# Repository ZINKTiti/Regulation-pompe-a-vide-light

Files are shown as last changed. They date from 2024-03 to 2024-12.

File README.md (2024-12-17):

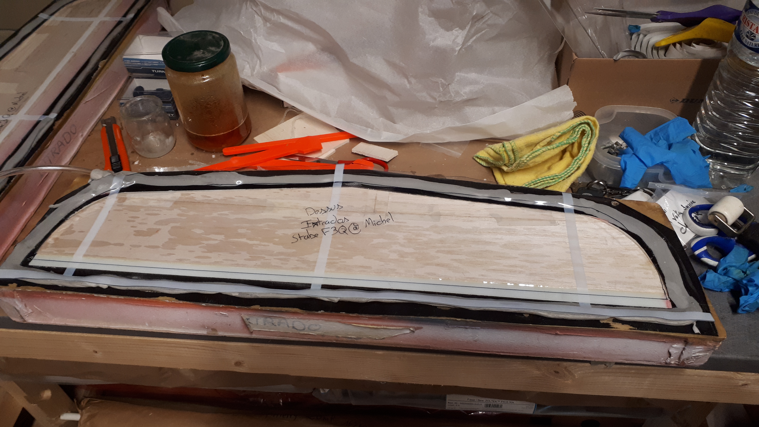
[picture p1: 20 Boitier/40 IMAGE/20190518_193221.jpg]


# ENGLISH

## Vaccum regulation

This is a light way to manage the vaccum pump to mold composit model aircraft

:warning: WARNING :warning: |
:--:|
**This assembly includes 220V connections. Take all safety measures to avoid any electrical shock that could cause irreversible bodily harm or even death.**|
**Never work on your assembly while it is live.**|

You can found the wiki  [Here](https://github.com/ZINKTiti/Regulation-pompe-a-vide-light/wiki)
The original is comming from [This](https://www.rcgroups.com/forums/showthread.php?2617244-Arduino-vacuum-pump-controller/page2)

---
---

# FRENCH

## Régulation de pompe a vide

Ce montage est un moyen de reguler le vide pour le moulage sous vide de model réduit

:warning: ATTENTION :warning: |
:--:|
**Ce montage comporte des connections en 220V. Prenez toutes les mesures de sécurité afin d'éviter tous choque éléctrique pouvant entrainer des domages corporels ireversible voir entrainer la mort**|
**Ne jamais intervenir sur votre montage sous tension**|

Vous pouvez trouver le wiki [ICI](https://github.com/ZINKTiti/Regulation-pompe-a-vide-light/wiki)
L'idée original viens de ce [cite](https://www.rcgroups.com/forums/showthread.php?2617244-Arduino-vacuum-pump-controller/page2)

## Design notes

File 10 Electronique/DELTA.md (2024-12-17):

# V1

Ajouter |
:--:|
Ajout de deux support à fusible protection primaire et secondaire|

Modifier |
:--:|
changement de Pin pour le DT de Pin4 à Pin3|
changement de Pin pour le CLK de Pin3 à Pin2|

Supprimer |
:--:|
|

# V0

Premire version

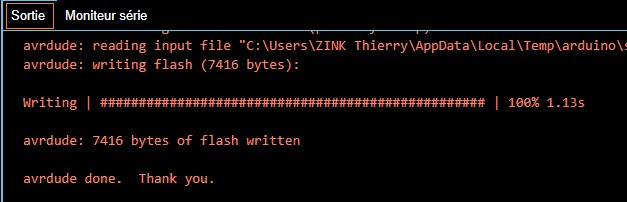
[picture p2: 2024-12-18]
25 Document/Chargement Fini.jpg

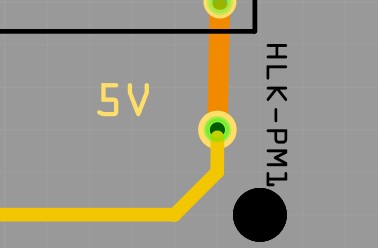
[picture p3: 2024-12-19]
25 Document/PCB_passage1.jpg

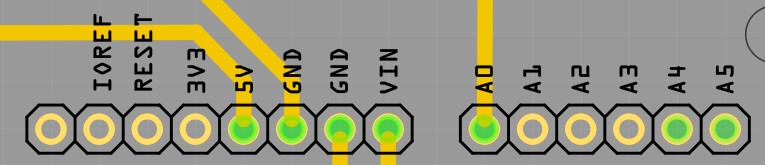
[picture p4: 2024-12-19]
25 Document/PCB_connecteur Arduino1.jpg

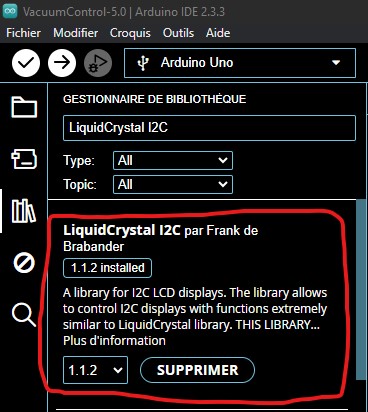
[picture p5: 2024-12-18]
25 Document/Liquid crystal Frank de brabander.jpg

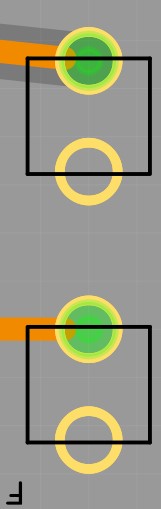
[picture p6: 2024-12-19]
25 Document/PCB_F1.jpg

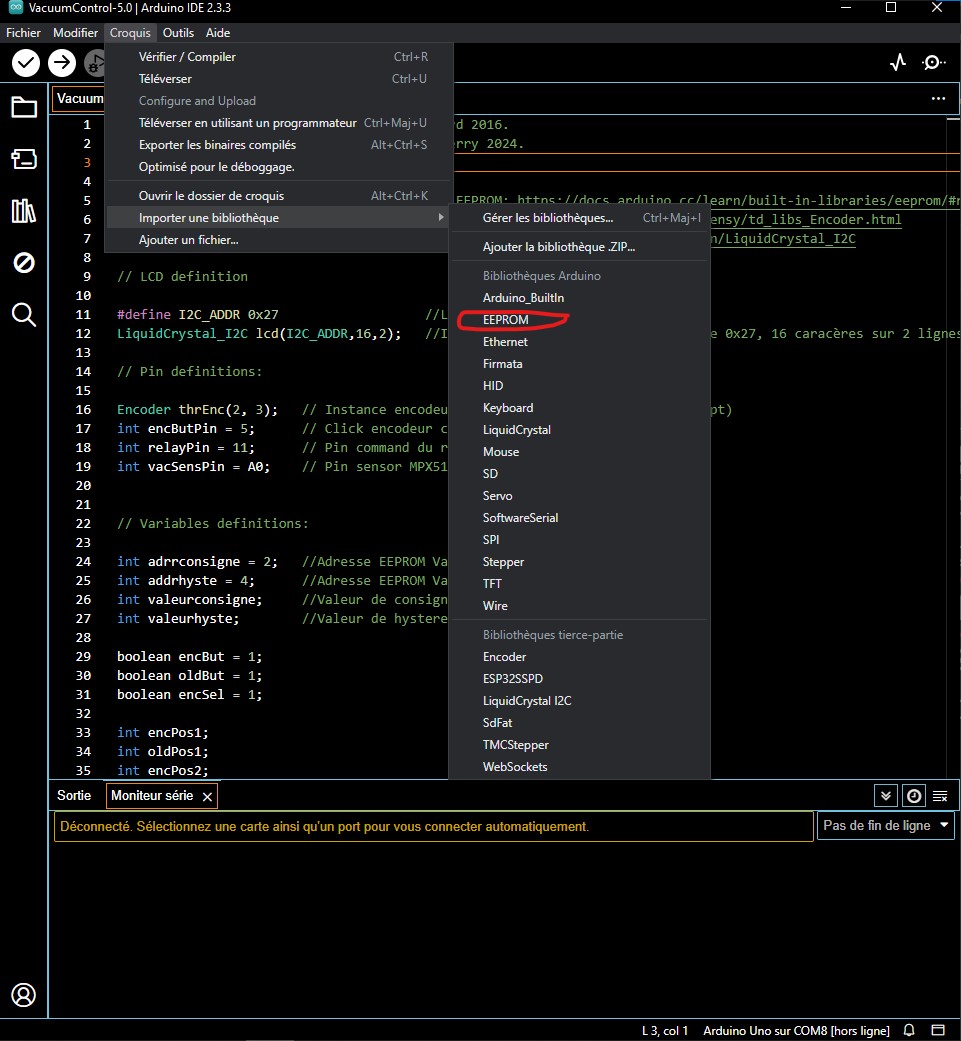
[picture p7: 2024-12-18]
25 Document/EEPROM.jpg

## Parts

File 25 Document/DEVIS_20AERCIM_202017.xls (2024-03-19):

Bruno REY |  |  |  |  |  |  | Devis
Bruno REY, AERCIM |  |  |  |  |  | le |  | N°
40 rue de la Providence
31500 | TOULOUSE
Téléphone | 05 61 20 69 57
 | 06 87 59 65 15
Email | aercim.ci@gmail.com
SIRET ; 803201680-00011 RM – RCS Toulouse
TVA non applicable, art 293B du CGI |  |  |  |  |  | www.aercim.com
toutes factures d'un montant inférieur à 100 euros sont à régler à la fin du mois en cours
 |  |  |  |  |  |  |  | d'avance merci
V/Réf: N°Cde:
Référence | Q | Nb Face | Dimensions |  | Trous | Descriptions |  | P.U | Montant
 | 4 | 2 | 10 | 6.7 | 62 |  |  | 7.02 | 28.09
 | 1 |  |  |  |  |  |  | 0.00 | 4.00
 |  |  |  |  |  | Frais de port/paypal |  |  | 3.00
 | Tarif surface |  | SF | 8 | euro/dcm² |  | Total |  | 35.09 | €
 | 2.7 | dm² | DF | 9 | euro/dcm² |  | acompte
 |  |  |  |  | franchise de TVA ; art 293B du CGI
chèques ; à l'ordre de Bruno REY |  |  |  |  |  |  | Total à régler |  | 35.09 | €
virement ; demander un RIB
paypal ; demande de paiement par email
 |  |  |  | Règlement
 |  |  |  | Échéance
En cas de retard de paiement, indemnité forfaitaire légale pour frais de recouvrement : 40,00 €
AERCIM : une électronique selon vos besoins.
Tout ou partie de votre projet ;
Du cahier des charges au produit fini, nous savons le faire.

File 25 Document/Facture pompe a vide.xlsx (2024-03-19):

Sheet: Sylvain
Pompe a vide
Designation | Prix unitaire | Quantité | Prix
CI | 13.25 | 1 | 13.25
MPX5100DP | 14.11 | 1 | 14.11
Aduino Uno | 8.99 | 1 | 8.99
2 pole | 1.43 | 1 | 1.43
Relais Statique | 9.8 | 1 | 9.8
LCD | 4.42 | 1 | 4.42
HLK-PM01 | 3.998 | 1 | 3.998
HY-040 | 2.3484 | 1 | 2.3484
Cable + prise | 5 | 1 | 5
Prise de courant | 3.9 | 1 | 3.9
Bois | 7.7 | 1 | 7.7
 |  |  | 0
Temps | 10 | 1 | 10
 |  |  | 0
 |  |  | 0
 |  |  | 0
 |  |  | 0
Total |  |  | 84.9464

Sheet: Jean Luc
Pompe a vide
Designation | Prix unitaire | Quantité | Prix
CI | 13.25 | 1 | 13.25
MPX5100DP | 13.99 | 1 | 13.99
Aduino Uno | 6.6 | 1 | 6.6
2 pole | 0.75 | 1 | 0.75
Relais Statique | 3.69 | 1 | 3.69
LCD | 4.34 | 1 | 4.34
HLK-PM01 | 3.998 | 1 | 3.998
HY-040 | 2.3484 | 1 | 2.3484
Cable + prise | 2 | 1 | 2
 |  |  | 0
 |  |  | 0
Temps | 10 | 1 | 10
 |  |  | 0
 |  |  | 0
 |  |  | 0
 |  |  | 0
 |  |  | 0
Total |  |  | 60.9664

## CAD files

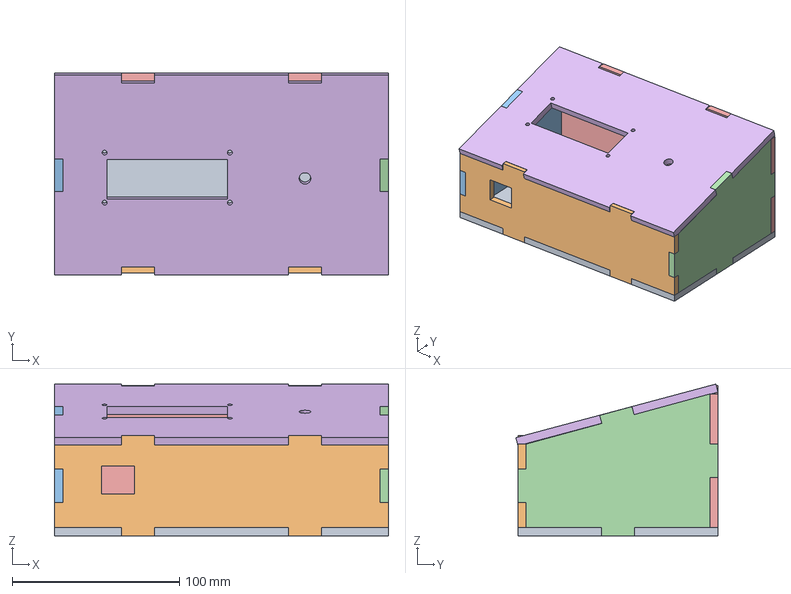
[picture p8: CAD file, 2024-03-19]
20 Boitier/10 FREECAD/boitier.FCStd
200.0 x 121.2 x 90.9 mm
Font
Avant
Coter
Arriere
Couvercle

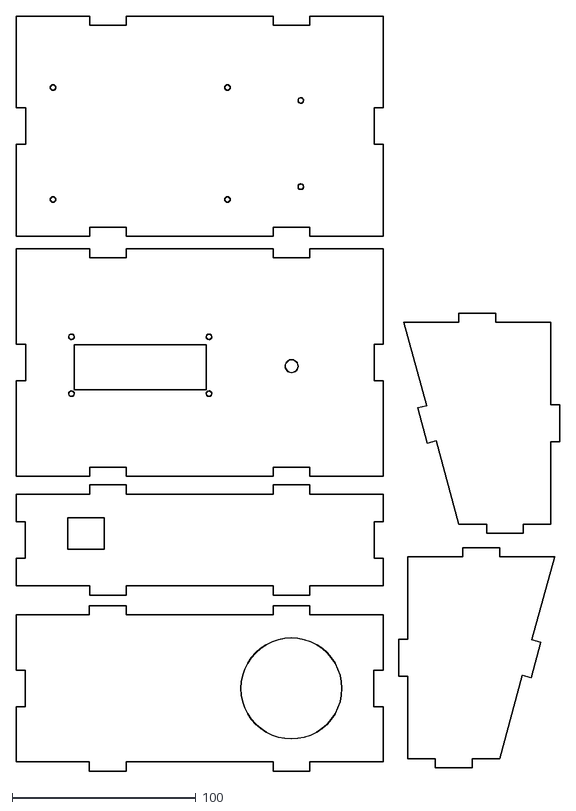
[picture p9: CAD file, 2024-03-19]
20 Boitier/20 INKSKAPE/10 Caplinage/Boitier.dxf
296.3 x 411.4

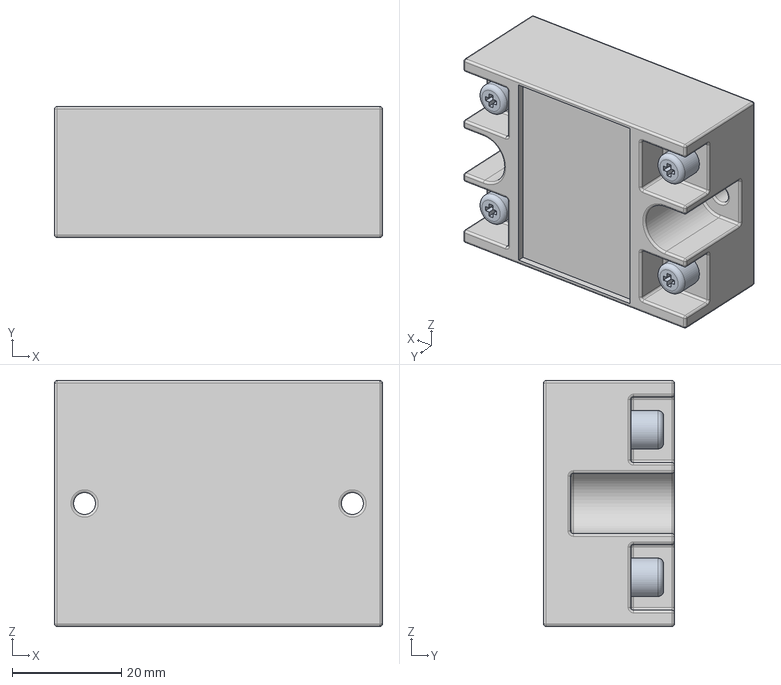
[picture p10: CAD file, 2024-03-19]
20 Boitier/10 FREECAD/Fotek_SSR-25_DA_v1.step
60.0 x 24.0 x 45.0 mm

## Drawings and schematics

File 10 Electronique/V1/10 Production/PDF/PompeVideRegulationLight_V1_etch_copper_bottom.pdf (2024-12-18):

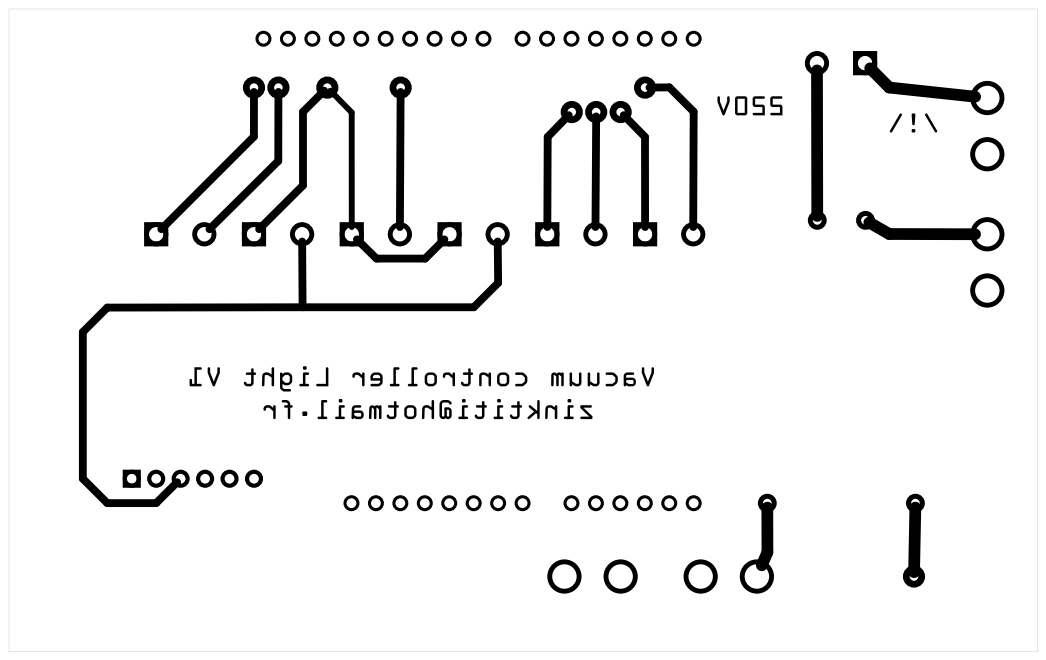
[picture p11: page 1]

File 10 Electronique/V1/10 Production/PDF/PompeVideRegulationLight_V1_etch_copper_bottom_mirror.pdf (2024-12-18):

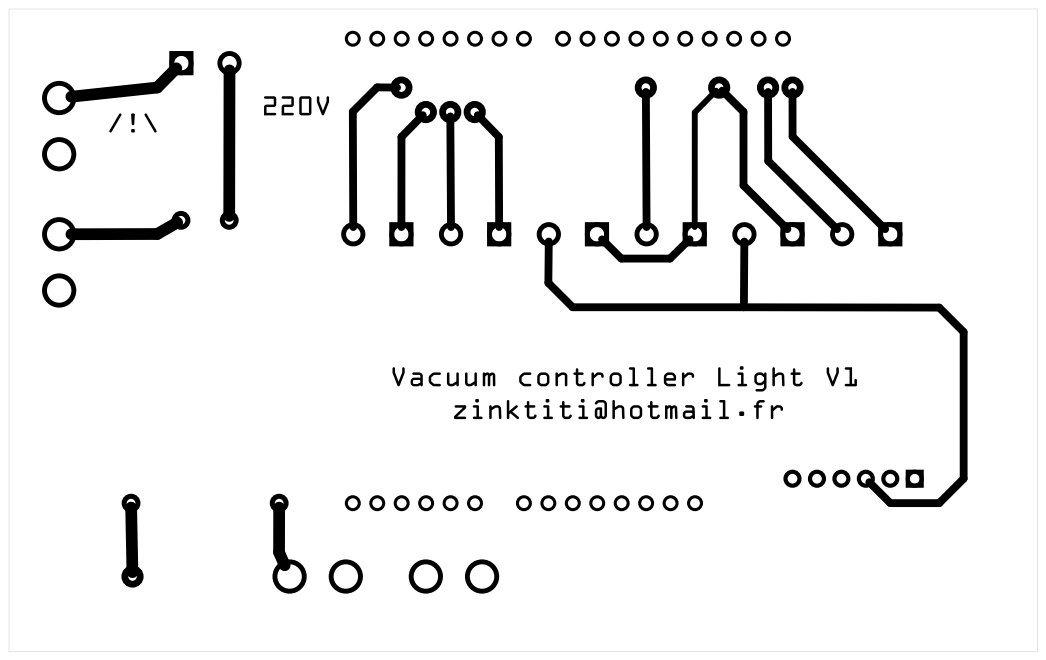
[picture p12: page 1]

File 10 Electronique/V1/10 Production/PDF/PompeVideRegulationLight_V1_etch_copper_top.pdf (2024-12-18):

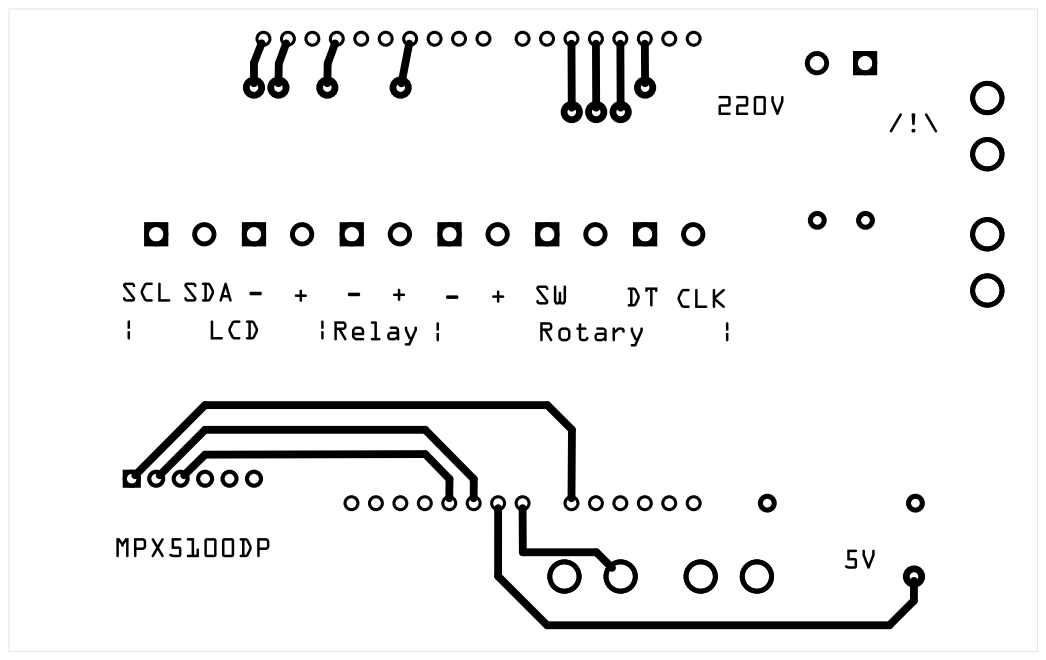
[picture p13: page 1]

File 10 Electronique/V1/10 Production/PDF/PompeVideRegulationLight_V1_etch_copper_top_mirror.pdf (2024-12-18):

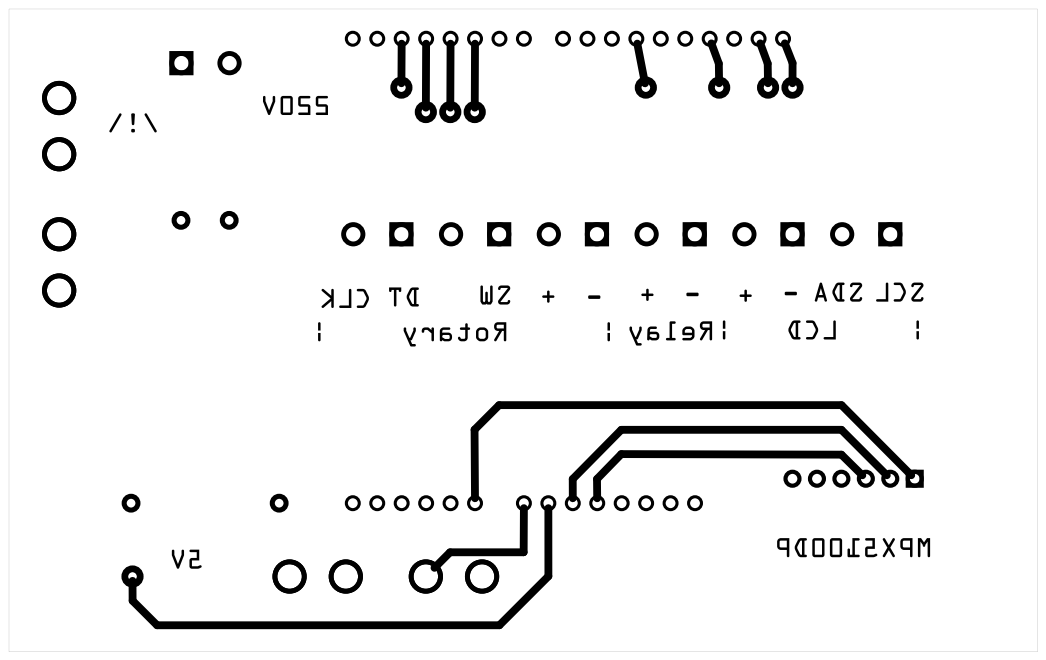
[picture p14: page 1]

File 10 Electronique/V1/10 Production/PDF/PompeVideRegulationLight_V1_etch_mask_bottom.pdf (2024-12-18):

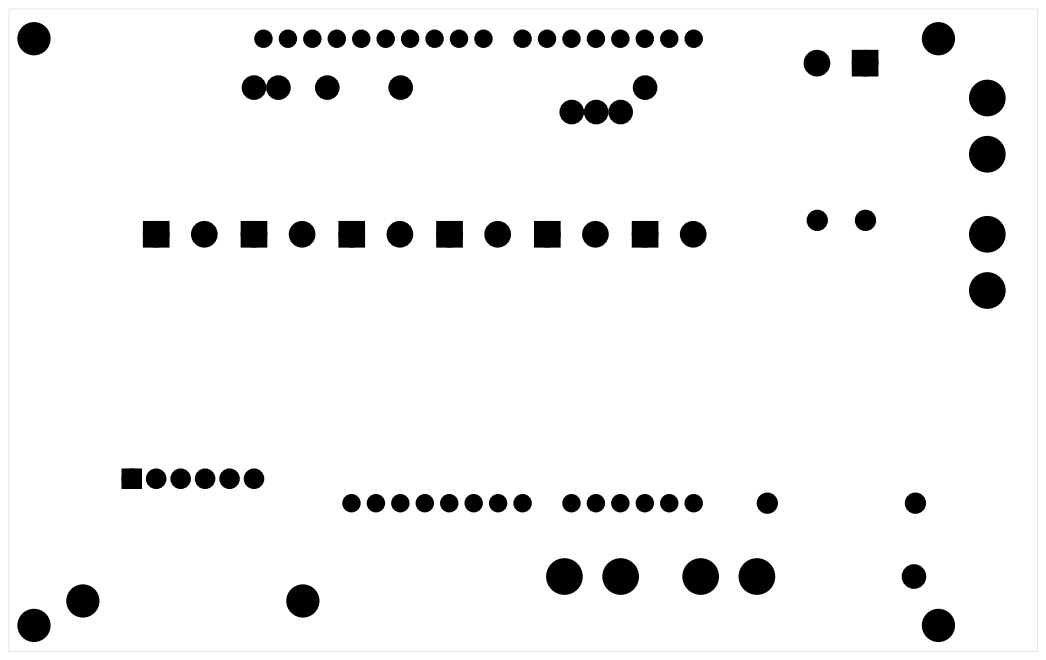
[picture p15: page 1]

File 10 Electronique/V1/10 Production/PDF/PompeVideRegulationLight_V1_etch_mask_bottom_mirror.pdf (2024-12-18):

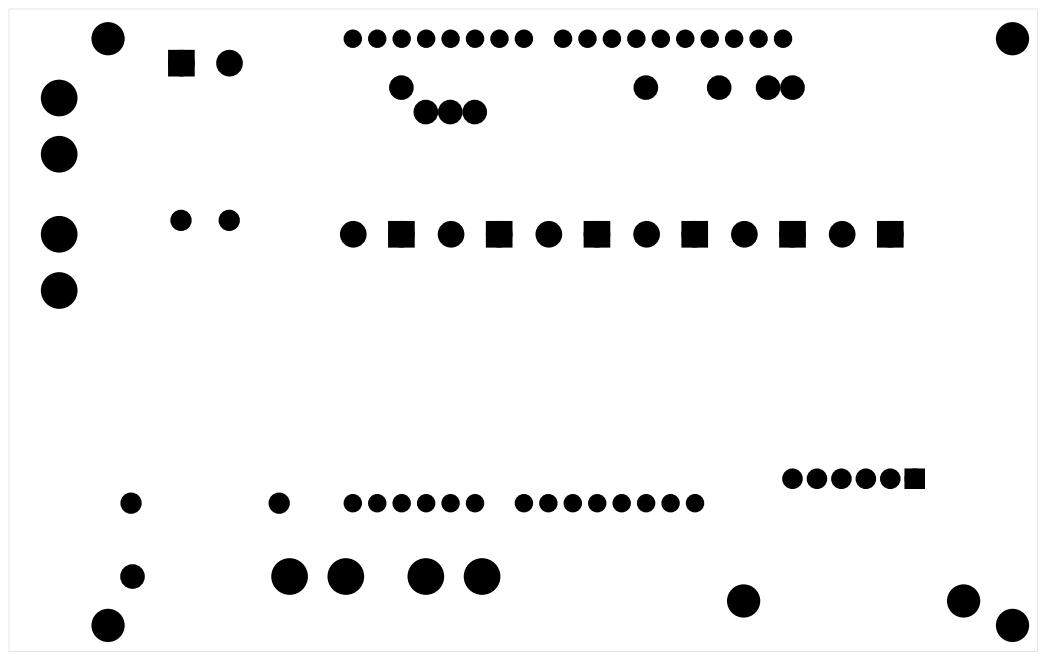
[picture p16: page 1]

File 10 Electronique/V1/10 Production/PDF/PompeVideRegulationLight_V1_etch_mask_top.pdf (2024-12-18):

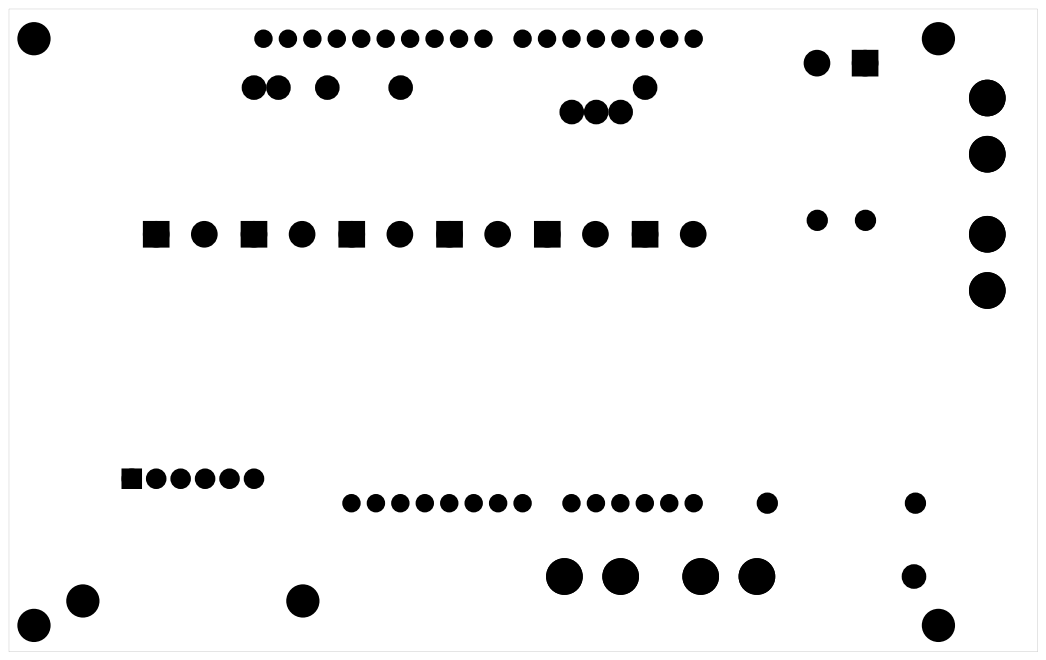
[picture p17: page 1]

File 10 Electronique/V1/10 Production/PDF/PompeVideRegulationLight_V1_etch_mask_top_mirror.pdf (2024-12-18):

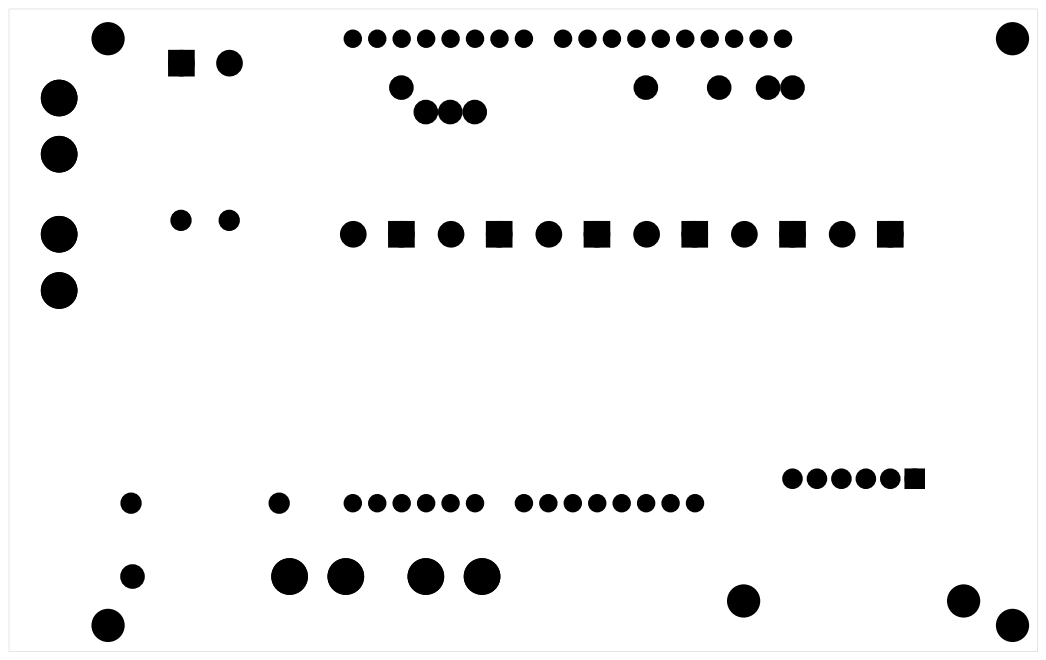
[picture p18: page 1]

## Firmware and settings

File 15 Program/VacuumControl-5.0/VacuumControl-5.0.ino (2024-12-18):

// Vacuum controller, origin Tryggve Kallhovd 2016.
// Vacuum Controller, modification ZINK Thierry 2024.


#include <EEPROM.h>               // Libray EEPROM: https://docs.arduino.cc/learn/built-in-libraries/eeprom/#read
#include <Encoder.h>              // Encoder Library: https://www.pjrc.com/teensy/td_libs_Encoder.html
#include <LiquidCrystal_I2C.h>    // Ecran LCD: https://github.com/johnrickman/LiquidCrystal_I2C

// Debug

boolean debug = 1;              // Mode Debug Valeur à 1 sinon 0  

// LCD definition

#define I2C_ADDR 0x27                   //Lcd i2c addresse 0x27
LiquidCrystal_I2C lcd(I2C_ADDR,16,2);   //Instance Afficheur LCD, i2c addresse 0x27, 16 caracères sur 2 lignes

// Pin definitions:

Encoder thrEnc(2, 3);   // Instance encodeur port 2 (interrupt) et 3 (interrupt)
int encButPin = 5;      // Click encodeur central
int relayPin = 11;      // Pin command du relay
int vacSensPin = A0;    // Pin sensor MPX5100_DP


// Variables definitions:

int adrrconsigne = 2;   //Adresse EEPROM Valeur Règlage 
int addrhyste = 4;      //Adresse EEPROM Valeur Marge
int valeurconsigne;     //Valeur de consigne
int valeurhyste;        //Valeur de hysteresise

boolean encBut = 1;
boolean oldBut = 1;
boolean encSel = 1;

int encPos1;
int oldPos1;
int encPos2;
int oldPos2;

boolean vacSwitch;

int vacuum;
int vacVal;
int oldVal;

// Fonctions definitions:

void writeIntIntoEEPROM(int address, int number)  // ecriture en memoire dun nombre number dans l'adresse address
{ 
  byte byte1 = number >> 8;           // Extraire l'octet de poids fort (octet le plus significatif)
  byte byte2 = number & 0xFF;         // Extraire l'octet de poids faible (octet le moins significatif)
  EEPROM.write(address, byte1);       // Écrire l'octet de poids fort dans l'EEPROM
  EEPROM.write(address + 1, byte2);   // Écrire l'octet de poids faible à l'adresse suivante
}

int readIntFromEEPROM(int address)                // lecture en memoire dun nombre number dans l'adresse address
{
  byte byte1 = EEPROM.read(address);      // Lire l'octet de poids fort
  byte byte2 = EEPROM.read(address + 1);  // Lire l'octet de poids faible
  return (byte1 << 8) | byte2;            // Combiner les deux octets pour reformer l'entier
}

void setup() {

  Serial.begin(9600);

  lcd.init();                     // initialize the lcd
  lcd.backlight();                // Allume le back light
  lcd.setCursor(0, 0);            // Position Ecriture colone 0 ligne 0
  lcd.print("Reglage:   -");      // Ecriture 
  lcd.setCursor(0, 1);            // Position Ecriture colone 0 ligne 0
  lcd.print("Mesure:");           // Ecriture
  lcd.setCursor(13, 1);           // Position Ecriture colone 13 ligne 1
  lcd.print("mBr");               // Ecriture

  //Initialisation par lecture des valeurs dans l'EEPROM
  
  valeurconsigne = readIntFromEEPROM(adrrconsigne); // Lecture de la valeur en mémoire dans l'adresse 1 du reglage
  valeurhyste = readIntFromEEPROM(addrhyste);       // Lecture de la valeur en mémoire dans l'adresse 2 de l'hysteresis
  encPos1 = (valeurconsigne* 4);
  encPos2 = (valeurhyste * 4);
  thrEnc.write(encPos1);

  // Initialisation des port
  
    // Configuration du bouton avec pull-up interne
  pinMode(encButPin, INPUT);
  digitalWrite(encButPin, HIGH);

    // Configuration du relais en sortie, désactivé au départ
  pinMode(relayPin, OUTPUT);
  digitalWrite(relayPin, LOW);

    // Configuration de la broche du capteur en entrée
  pinMode(vacSensPin, INPUT);
  
}

void loop() {

  // Analyse le Bouton de l'encodeur:
  // change entre "Règlage" (la consigne) et "Marge" (l'hystérésis) à chaque appui
  // encSel = 1 affiche la consigne
  // encSel = 0 affiche l'hystérésis
  // Sur l'afficheur en ligne 0 affichage de la consigne et d l'hystérésis alternativement
  // La valeur affichée peut être ajustée avec l'encodeur
  // Sur l'afficheur en ligne 1 affichage de la valeur mesurée

  encBut = digitalRead(encButPin);
  if (encBut != oldBut) {         // Vérifie s'il y a un changement d'état
    if (encBut == 0) {
      encSel = !encSel;           // Bascule la valeur de encSel
    }
    if (encSel == 1) {            // Affiche la consigne
      thrEnc.write(encPos1);
      lcd.setCursor(0, 0);
      lcd.print("Reglage:   -");

    } else if (encSel == 0) {     //Affiche l'hystérésis
      thrEnc.write(encPos2);
      lcd.setCursor(0, 0);
      lcd.print("Marge:  +/- ");
      lcd.setCursor(14, 0);
      lcd.print(" ");
    }
    oldBut = encBut;              // Met à jour l'état précédent du bouton
  }

  // Lecture de l'encodeur:

  if (encSel) {
    encPos1 = thrEnc.read();
    if (encPos1 != oldPos1) {
      oldPos1 = encPos1;
    }
    
    // Si l'encodeur a été tourné et encSel = 1 (Régage de la consigne)
    // Test des valeurs limites de la consigne qui doit être >= 10 et <= 99
    // Si en dehors des limites la consigne est mis à la limite correspondante
    if (encPos1 >= (99 * 4)) {
      encPos1 = (99 * 4);
      thrEnc.write(99 * 4);
    } else if (encPos1 <= (10 * 4)) {
      encPos1 = (10 * 4);
      thrEnc.write(10 * 4);
    }
    
    // La consigne est mise en mémoire dans l'EEPROM et affichée
    int val = ((encPos1) / 4);
    writeIntIntoEEPROM(adrrconsigne, val);
    lcd.setCursor(12, 0);
    lcd.print((encPos1 / 4) * 10);
  }
  else  {
    encPos2 = thrEnc.read();
    if (encPos2 != oldPos2) {
      oldPos2 = encPos2;
    }

    // Si l'encodeur a été tourné et encSel = 0 (Régage de l'hystérésis)
    // Test des valeurs limites de l'hystérésis qui doit être >= 5 et <= 50
    // Si en dehors des limites l'hystérésis est mise à la limite correspondante  
    if (encPos2 >= (50 * 4)) {
      encPos2 = (50 * 4);
      thrEnc.write(50 * 4);
    } else if (encPos2 <= (5 * 4)) {
      encPos2 = (5 * 4);
      thrEnc.write(5 * 4);
    }
    
    // La valeur de l'hystérésis est mise en mémoire dans l'EEPROM et affichée
    int val = ((encPos2) / 4);
    writeIntIntoEEPROM(addrhyste, val);
    lcd.setCursor(12, 0);
    lcd.print(encPos2 / 4);
    if ((encPos2 / 4) < 10) {
      lcd.setCursor(13, 0);
      lcd.print(" ");
    }
  }

  // Contrôle du relai en fonction de la valeur de vide mesurée, de la consigne "encPos1" et de l'hytérésis "encPos2":

  if (vacSwitch == 1) {
    if (vacuum >= ((encPos1 / 4) * 10) + (encPos2 / 4)) {
      vacSwitch = 0;
    }
  } else if (vacSwitch == 0) {
    if (vacuum < ((encPos1 / 4) * 10) - (encPos2 / 4)) {
      vacSwitch = 1;
    }
    digitalWrite(relayPin, vacSwitch);
  }

  // mesure de la valeur avec le capteur MPX5100DP

  vacuum = 0;
  
  // mesure de 10 valeurs du vide
  for (byte i = 0; i < 10; i++) {
    vacuum += analogRead(vacSensPin);
  }
  vacuum /= 10;
  
  // Mise à l'échelle réelle
  vacuum = map(vacuum, 41, 962, 0, 1000);

  // Moyennage avec la valeur précédent
  vacVal = (vacuum + oldVal) / 2;
  oldVal = vacVal;
  if (vacVal < 1) {
    vacVal = 0;
  }
  
  // Affichage de la nouvelle valeur

  lcd.setCursor(9, 1);
  lcd.print(vacVal);
    if (vacVal > 0) {
    lcd.setCursor(8, 1);
    lcd.print("-");
  } else {
    lcd.setCursor(8, 1);
    lcd.print(" ");
  }
  if (vacVal < 10) {
    lcd.setCursor(10, 1);
    lcd.print(" ");
  } else if (vacVal < 100) {
    lcd.setCursor(11, 1);
    lcd.print(" ");
  }

  // Debug

  if (debug=1) {
    Serial.print("Sensor:");
    Serial.print(vacVal);
    Serial.print("_");
    Serial.print("Consigne Enc:");
    Serial.print(encPos1);
    Serial.print("_");
    Serial.print("Consigne Hyst:");
    Serial.print(encPos2);
    Serial.print("_");
    Serial.print("Etat Relay:");
    Serial.print(vacSwitch);
    Serial.print("_");
    Serial.print("EEPROM Consigne:");
    Serial.print(readIntFromEEPROM(adrrconsigne));
    Serial.print("_");
    Serial.print(EEPROM.read(2));
    Serial.print("/");
    Serial.print(EEPROM.read(3));
    Serial.print("_");
    Serial.print("EEPROM Hyste:");
    Serial.print(readIntFromEEPROM(addrhyste));
    Serial.print("_");
    Serial.print(EEPROM.read(4));
    Serial.print("/");
    Serial.println(EEPROM.read(5));
  }
}

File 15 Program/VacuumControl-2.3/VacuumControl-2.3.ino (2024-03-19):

// Vacuum controller, Tryggve Kallhovd 2016.
// Encoder Library: https://www.pjrc.com/teensy/td_libs_Encoder.html

#include <EEPROM.h>
//#include <LiquidCrystal.h>

#include <Encoder.h>

#include <LCD.h>
#include <LiquidCrystal_I2C.h>

#define I2C_ADDR 0x27
#define BACKLIGHT_PIN 3
#define En_pin 2
#define Rw_pin 1
#define Rs_pin 0
#define D4_pin 4
#define D5_pin 5
#define D6_pin 6
#define D7_pin 7

LiquidCrystal_I2C lcd(I2C_ADDR,En_pin,Rw_pin,Rs_pin,D4_pin,D5_pin,D6_pin,D7_pin);

// Pin definitions:

Encoder thrEnc(3, 4);
int encButPin = 5;

int relayPin = 11;

int vacSensPin = A0;


// Function definitions:

int addr1 = 0;
int addr2 = 1;
byte value1;
byte value2;

boolean encBut;
boolean oldBut;
boolean encSel = 1;

int encPos1;
int oldPos1;
int encPos2;
int oldPos2;

boolean vacSwitch;

int vacuum;
int vacVal;
int oldVal;


void setup() {

  Serial.begin(9600);

  lcd.begin (16,2);
  lcd.setBacklightPin(BACKLIGHT_PIN,POSITIVE);
  lcd.setBacklight(HIGH);
  lcd.setCursor(0, 1);
  //lcd.print("Vacuum:");
  lcd.print("Mesure:");
  lcd.setCursor(13, 1);
  lcd.print("mBr");

  value1 = EEPROM.read(0);
  value2 = EEPROM.read(1);
  encPos1 = (value1 * 4);
  encPos2 = (value2 * 4);

  pinMode(encButPin, INPUT);
  digitalWrite(encButPin, HIGH);

  pinMode(relayPin, OUTPUT);
  digitalWrite(relayPin, LOW);

  pinMode(vacSensPin, INPUT);

  // initialize the lcd
  //lcd.init();

  // Print a message to the LCD.
  lcd.backlight();

}
void loop() {

  // Toggle encoder:

  encBut = digitalRead(encButPin);
  if (encBut != oldBut) {
    if (encBut == 0) {
      encSel = !encSel;
    }
    if (encSel == 1) {
      thrEnc.write(encPos1);
      lcd.setCursor(0, 0);
      //lcd.print("Threshold: -");
      lcd.print("Reglage:   -");

    } else if (encSel == 0) {
      thrEnc.write(encPos2);
      lcd.setCursor(0, 0);
      //lcd.print("Margin: +/- ");
      lcd.print("Marge:  +/- ");
      lcd.setCursor(14, 0);
      lcd.print(" ");
    }
    oldBut = encBut;
  }

  // Encoder:

  if (encSel) {
    encPos1 = thrEnc.read();
    if (encPos1 != oldPos1) {
      oldPos1 = encPos1;
    }
    if (encPos1 >= (99 * 4)) {
      encPos1 = (99 * 4);
      thrEnc.write(99 * 4);
    } else if (encPos1 <= (10 * 4)) {
      encPos1 = (10 * 4);
      thrEnc.write(10 * 4);
    }
    int val = ((encPos1) / 4);
    EEPROM.write(addr1, val);
    lcd.setCursor(12, 0);
    lcd.print((encPos1 / 4) * 10);
  }
  else  {
    encPos2 = thrEnc.read();
    if (encPos2 != oldPos2) {
      oldPos2 = encPos2;
    }
    if (encPos2 >= (50 * 4)) {
      encPos2 = (50 * 4);
      thrEnc.write(50 * 4);
    } else if (encPos2 <= (5 * 4)) {
      encPos2 = (5 * 4);
      thrEnc.write(5 * 4);
    }
    int val = ((encPos2) / 4);
    EEPROM.write(addr2, val);
    lcd.setCursor(12, 0);
    lcd.print(encPos2 / 4);
    if ((encPos2 / 4) < 10) {
      lcd.setCursor(13, 0);
      lcd.print(" ");
    }
  }

  // Vacuum switch:

  if (vacSwitch == 1) {
    if (vacuum >= ((encPos1 / 4) * 10) + (encPos2 / 4)) {
      vacSwitch = 0;
    }
  } else if (vacSwitch == 0) {
    if (vacuum < ((encPos1 / 4) * 10) - (encPos2 / 4)) {
      vacSwitch = 1;
    }
    digitalWrite(relayPin, vacSwitch);
  }

  // Vacuum sensor: (MPX5100DP)

  vacuum = 0;
  for (byte i = 0; i < 10; i++) {
    vacuum += analogRead(vacSensPin);
  }
  vacuum /= 10;
  vacuum = map(vacuum, 41, 962, 0, 1000);

  vacVal = (vacuum + oldVal) / 2;
  oldVal = vacVal;
  if (vacVal < 1) {
    vacVal = 0;
  }
  lcd.setCursor(9, 1);
  lcd.print(vacVal);
  Serial.println(vacVal);
  if (vacVal > 0) {
    lcd.setCursor(8, 1);
    lcd.print("-");
  } else {
    lcd.setCursor(8, 1);
    lcd.print(" ");
  }
  if (vacVal < 10) {
    lcd.setCursor(10, 1);
    lcd.print(" ");
  } else if (vacVal < 100) {
    lcd.setCursor(11, 1);
    lcd.print(" ");
  }
}

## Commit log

2024-03-19 New Commit
    [Boitier.dxf, DEVIS_20AERCIM_202017.xls, Facture pompe a vide.xlsx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]
2024-03-24 Modification PIN Bouton
    Modification PIN bouton pour les interuptes
    [Pompe a vide.xlsx, PompeVideRegulationLight_V0.fzz, PompeVideRegulationLight_V1.fzz]
2024-03-25 Correct PIN Rotacteur
    [PompeVideRegulationLight_V1.fzz]
2024-12-17 Modif Read et orga fichier
    [DEVIS_20AERCIM_202017.xls, Facture pompe a vide.xlsx, Pompe a vide.xlsx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]
2024-12-17 Update
    Bug for init at loading
    [VacuumControl-5.0.ino]
2024-12-19 Image PCB
2024-12-19 update Fritzing
    [PompeVideRegulationLight_V1.fzz]
